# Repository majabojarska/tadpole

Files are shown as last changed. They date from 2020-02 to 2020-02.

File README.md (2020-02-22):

# Tadpole
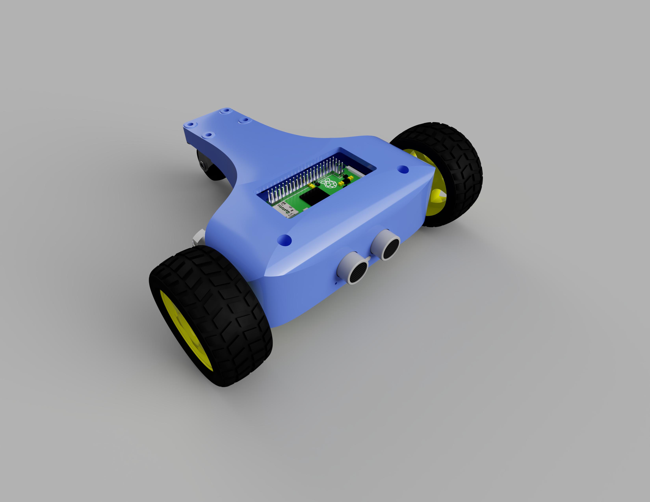
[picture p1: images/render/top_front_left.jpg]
Tadpole render


# About
Tadpole is a three-wheeled vehicle, driven by two indepedent front motors. My goal was to have a go at designing and integrating a system that consists of different software and hardware components.

A particularly interesting part of the design process, was implementing the motor controller logic, which handles conversion of user input, into motor speed and direction. The usage of two, independently driven front motors, enables the vehicle to not only turn while moving forwards/backwards, but also to spin in place. The calculated throttle (by default) is mapped to a 3rd order polynomial curve. This solution makes small movements result in subtle speed changes, but as the gamepad stick deviates further from its origin, the speed changes are more noticeable and aggressive. These characteristics make Tadpole particularly agile and precise.

## Hardware
Apart from te 3D printed stuff, the hardware parts are commonly available and can be cheaply ordered from online electronics shops. 

- Raspberry Pi Zero W
- 2x [6V DC motor](https://www.google.com/search?q=6v+dc+motor+robot+yellow).
- 2x 18650 battery.
- TP4056 battery charging and overdischarge protection module.
- DC-DC 5V booster module (RPi power source).
- DC-DC switching booster module (motor power source). 
- L9110S H-bridge motor driver.
- HC-SR04 ultrasonic sensor.
- Rotating furniture wheel.
- 3D printed frame.
- Xbox One S wireless gamepad.
- Some wires, soldering tools, screwdrivers, etc..

### 3D printing BOM
| Part ID | Amount (pcs)  |
| ---:|:---|
| cover_back.stl | 1 |
| cover_top.stl | 1 |
| frame_main.stl | 1 |
| mount_rpi.stl | 1 |

## Software
- [Raspbian Buster Lite](https://www.raspberrypi.org/downloads/raspbian/)
- [xpadneo](https://github.com/atar-axis/xpadneo) - Advanced Linux Driver for Xbox One Wireless Controller
- Python 3.6+ environment
- (optional) [Fusion 360, for tweaking the existing 3D project.](https://www.autodesk.com/products/fusion-360/overview)

## 3D Models
3D models are available in STL format under the [/models](./models) directory.
- Dummy models [/models/dummy](./models/dummy)
- Tadpole parts models [/models/tadpole](./models/tadpole)

## Circuit schematics
Circuit schematics in different file formats are located in the [/schematics](./schematics) directory.

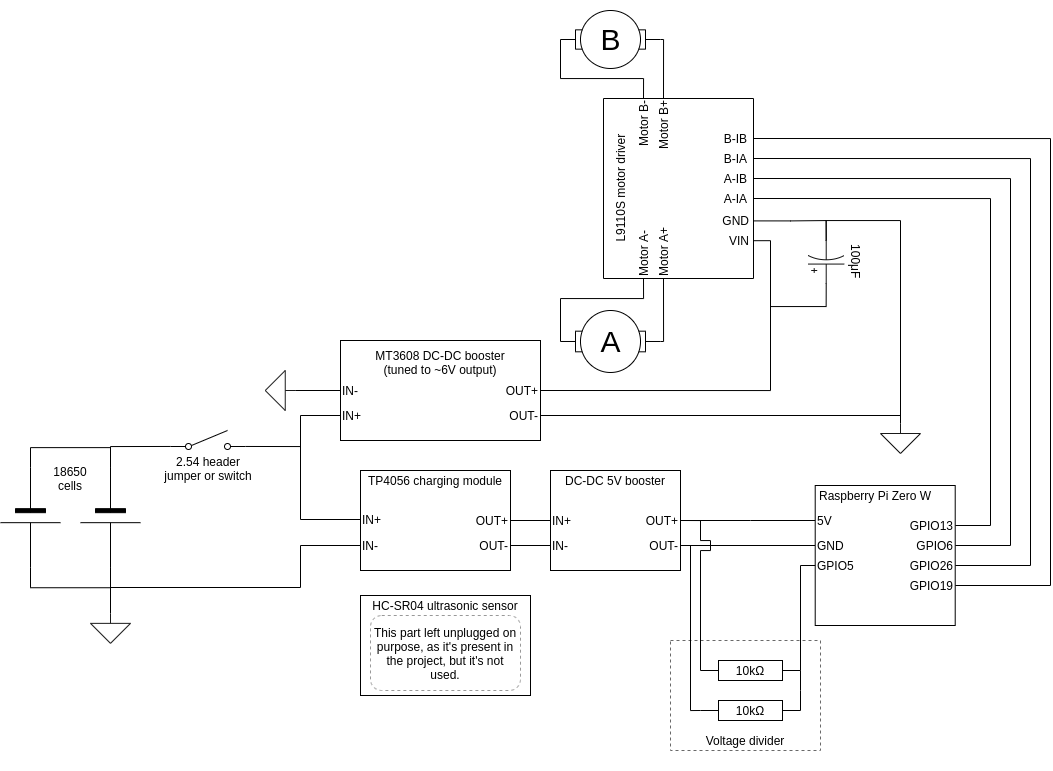
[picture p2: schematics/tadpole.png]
Tadpole schematic


## Images

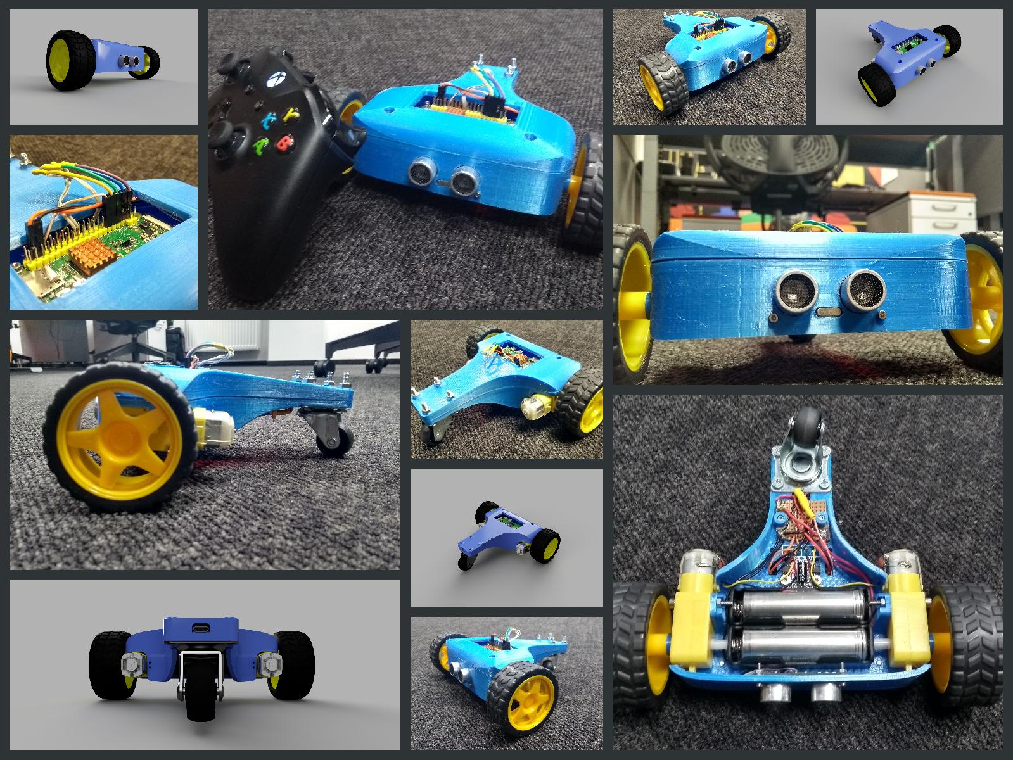
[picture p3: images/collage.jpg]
Tadpole images
Rendered images as well as real life photos can be found in the [images/](./images) directory.

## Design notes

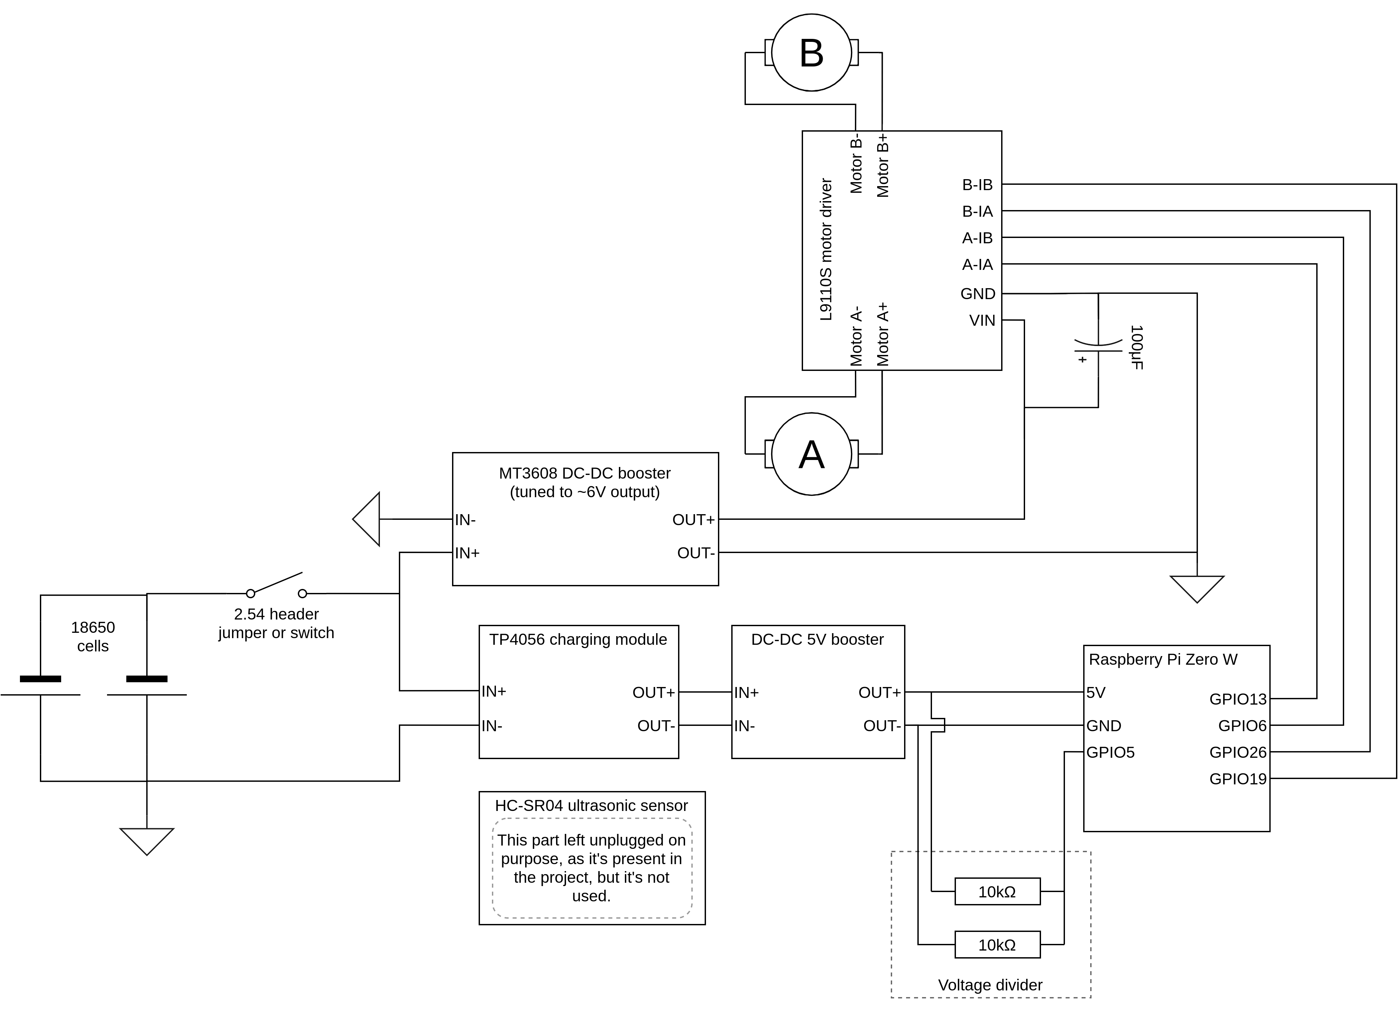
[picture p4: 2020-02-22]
schematics/tadpole_hi_res.png

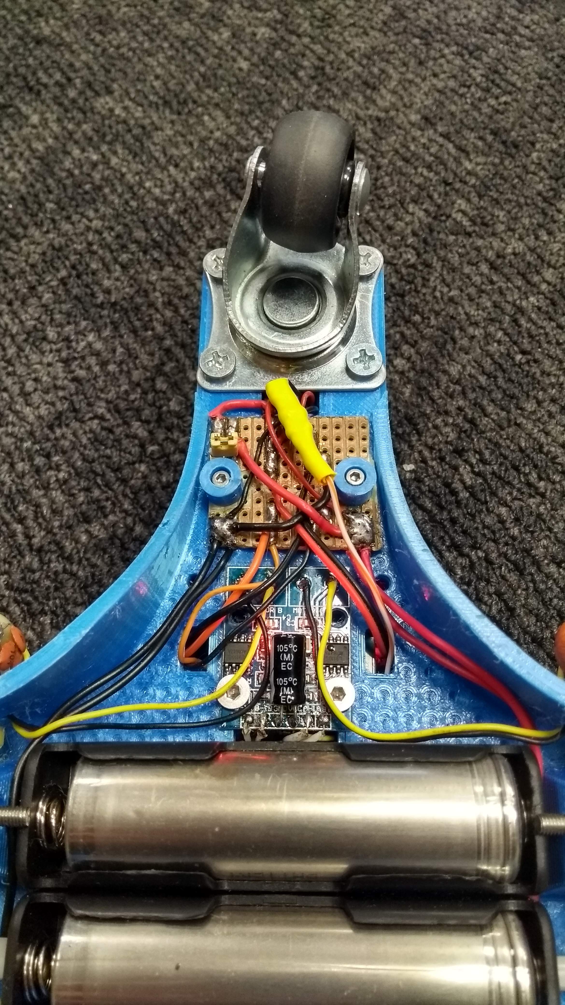
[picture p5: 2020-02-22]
images/photo/tadpole_14.jpg

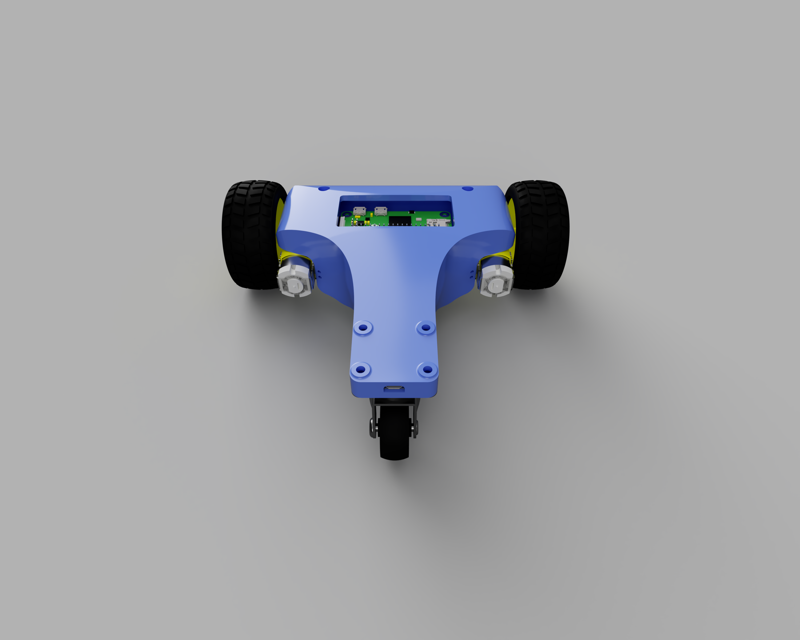
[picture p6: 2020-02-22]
images/render/top_back.png

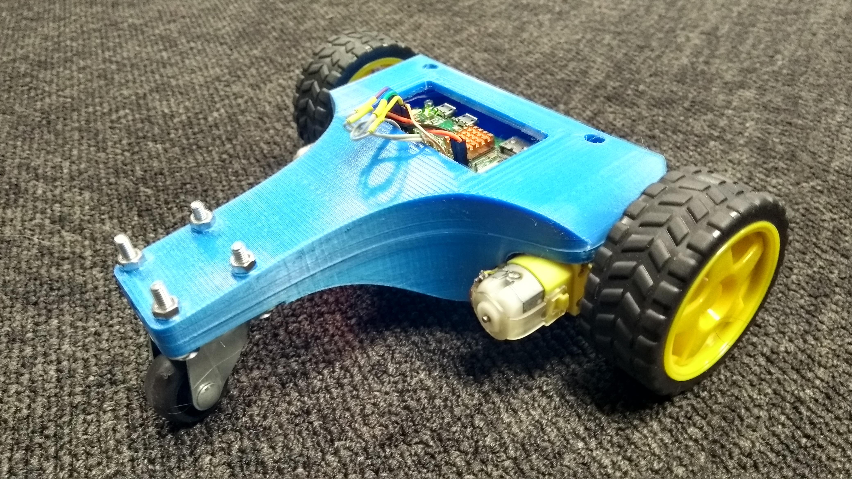
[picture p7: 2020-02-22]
images/photo/tadpole_07.jpg

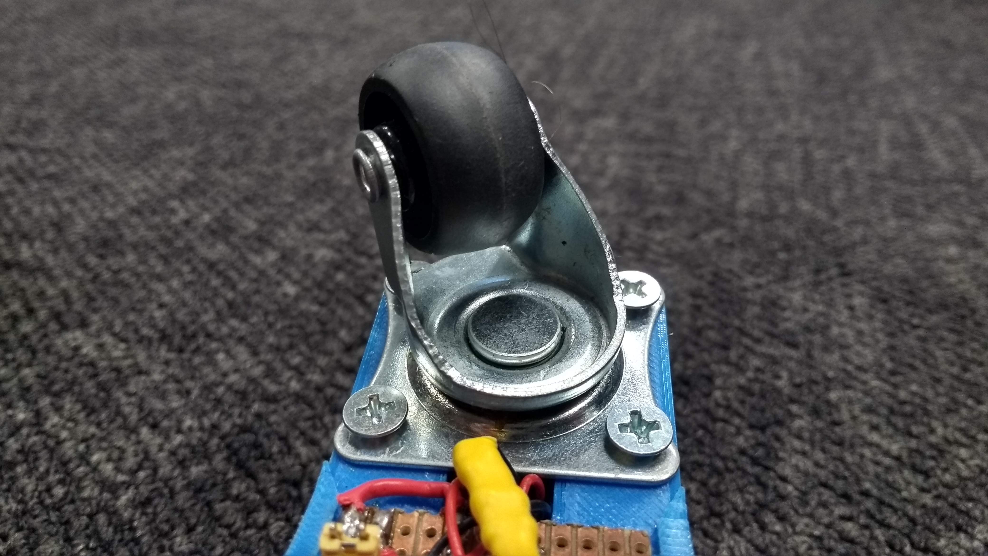
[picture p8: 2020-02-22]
images/photo/tadpole_17.jpg

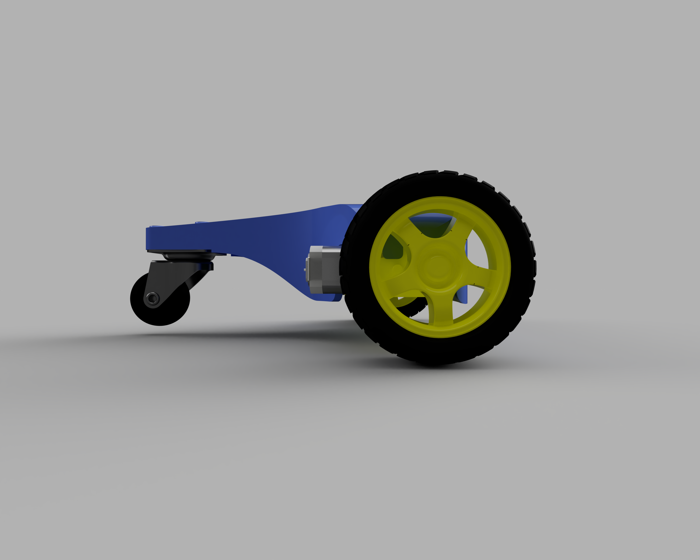
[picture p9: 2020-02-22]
images/render/right.png

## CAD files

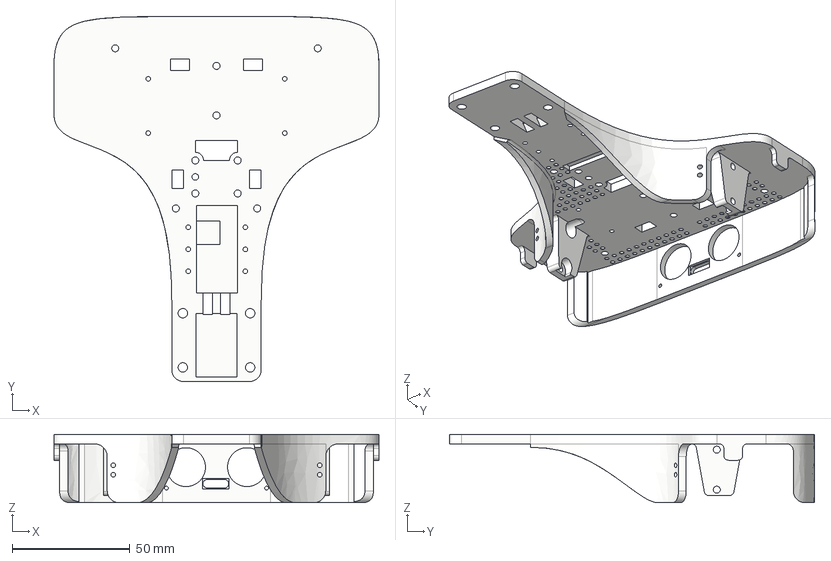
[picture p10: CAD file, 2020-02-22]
models/tadpole/step/frame_main.step
138.0 x 155.0 x 29.0 mm

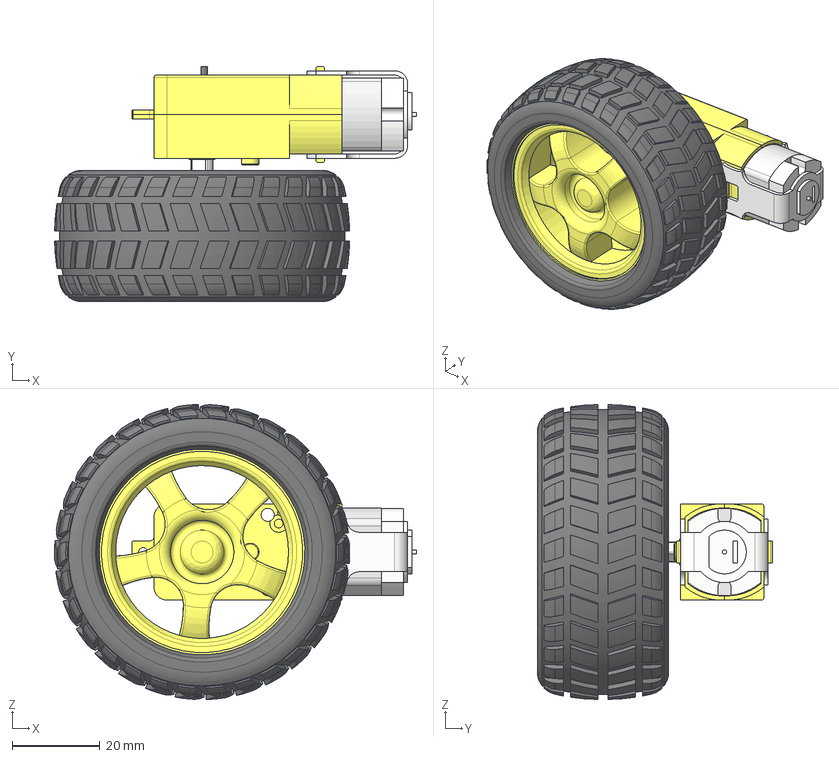
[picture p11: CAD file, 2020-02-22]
models/dummy/dc_motor_with_wheel.stp
82.7 x 53.8 x 67.5 mm
Wheel
capa 1 (amarela)
pino 2 (cinza)
capa 2 (amarela)
pino motor
base1 (cinza)
Ponta (preto)
suporte motor (acrílico)

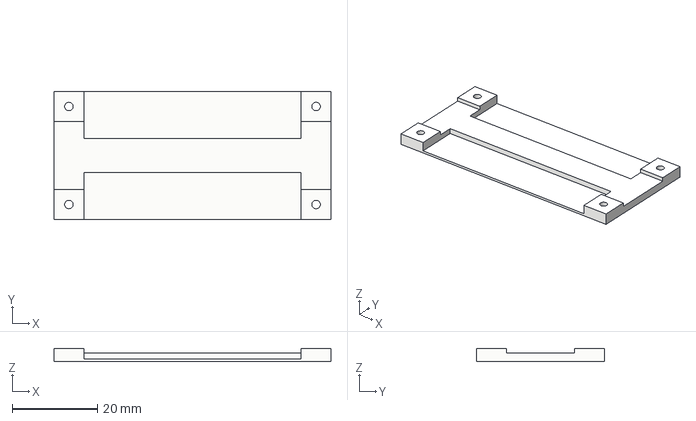
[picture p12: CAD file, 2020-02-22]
models/tadpole/step/mount_rpi.step
65.0 x 30.0 x 3.00 mm

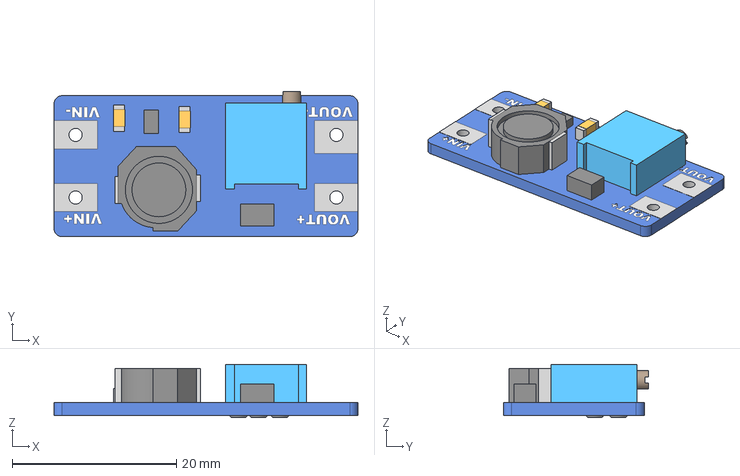
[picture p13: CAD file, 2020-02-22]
models/dummy/mt3608_module.stp
37.0 x 17.7 x 6.50 mm

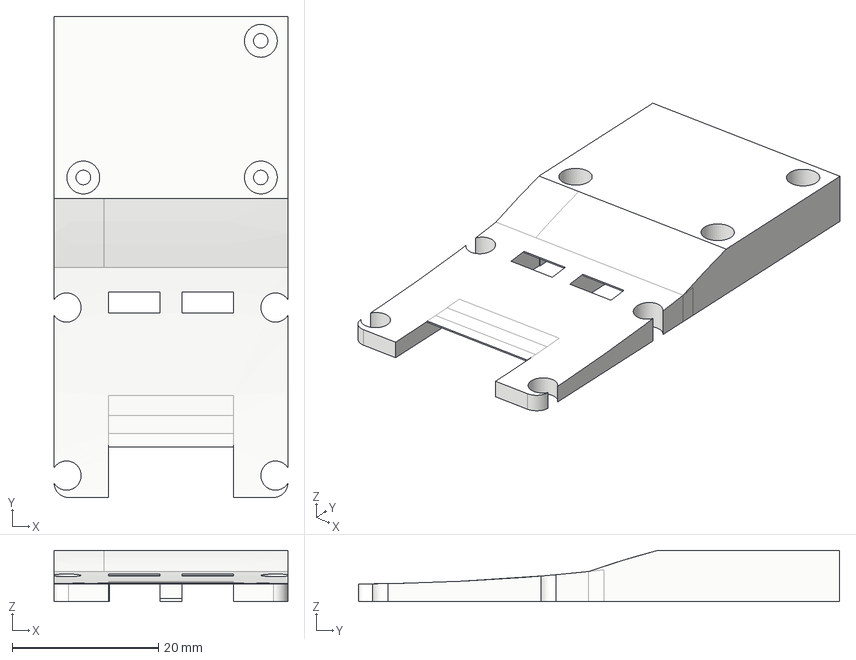
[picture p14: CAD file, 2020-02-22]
models/tadpole/step/cover_back.step
32.0 x 65.8 x 7.00 mm

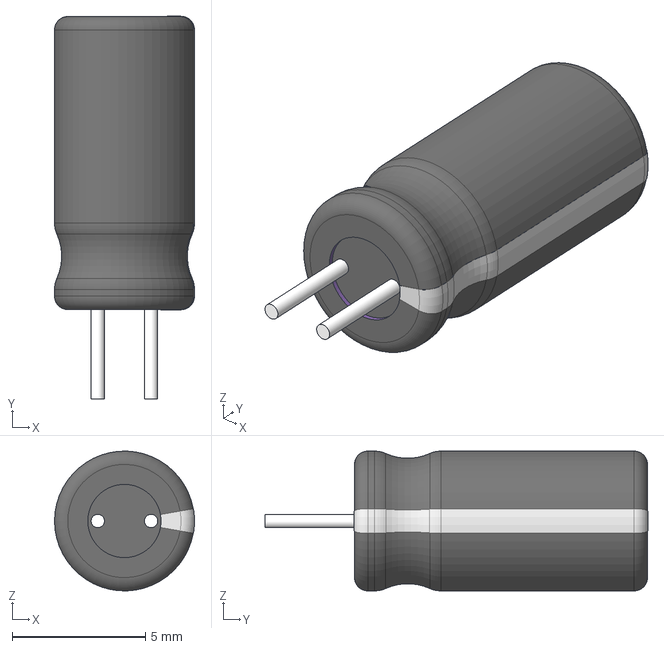
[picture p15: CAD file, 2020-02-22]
models/dummy/capacitor_electrolytic.stp
5.26 x 14.4 x 5.25 mm

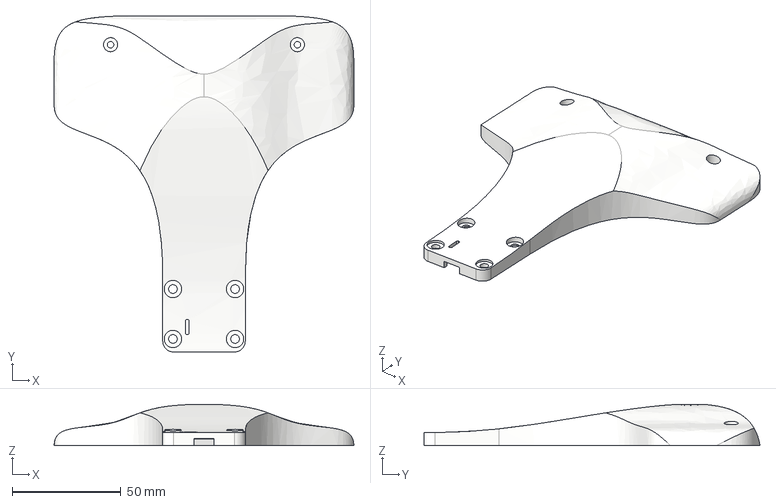
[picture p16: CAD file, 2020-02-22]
models/tadpole/step/cover_top.step
138.0 x 154.7 x 19.1 mm

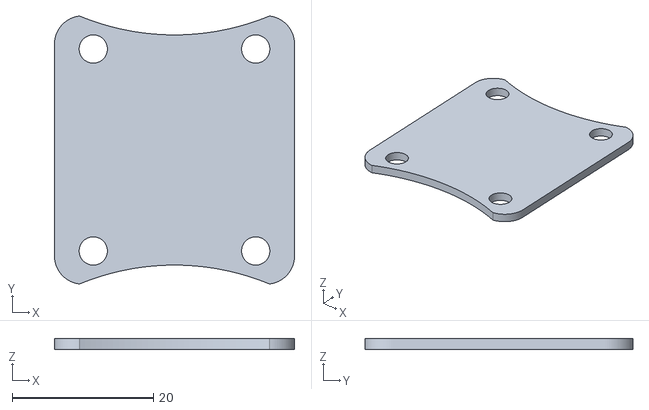
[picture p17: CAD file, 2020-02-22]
models/dummy/tail_wheel_plate.stl
34.0 x 38.0 x 1.50

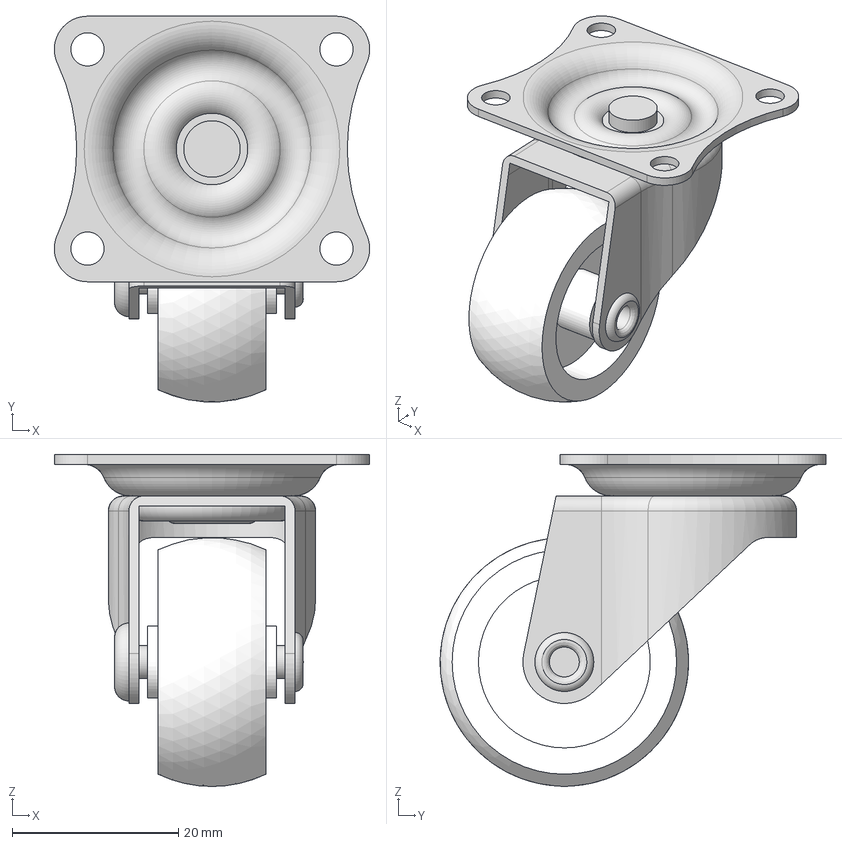
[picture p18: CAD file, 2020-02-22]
models/dummy/wheel_caster_swivel_40mm.stp
38.0 x 46.5 x 40.0 mm
Caster_40mm_Wheel_30mm_01
Caster_40mm_Wheel_support_01
Caster_40mm_Swivel_plate_01

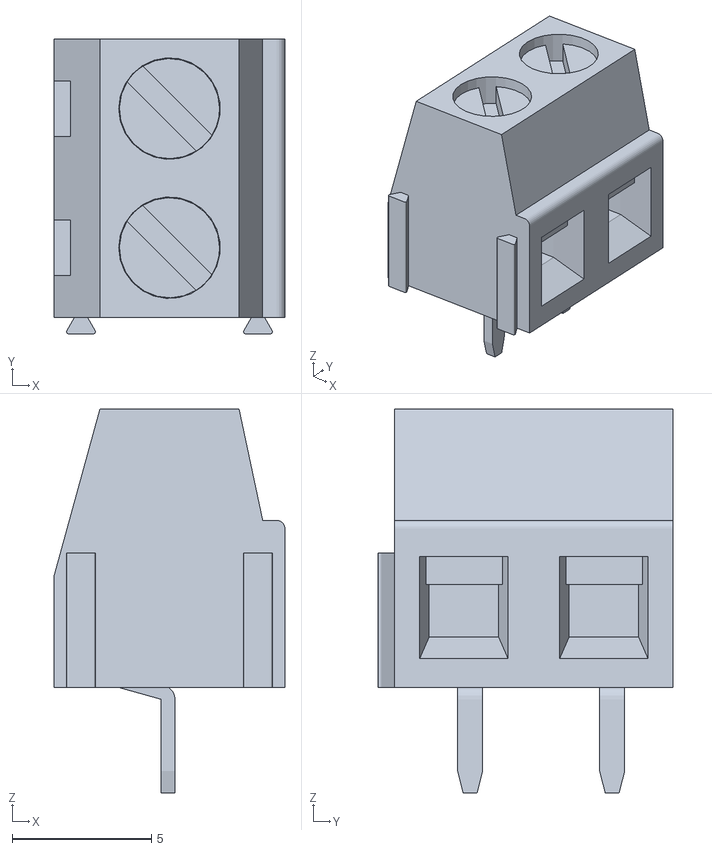
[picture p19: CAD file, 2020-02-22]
models/dummy/pcb_terminal_block_1x2.stl
8.30 x 10.6 x 13.8

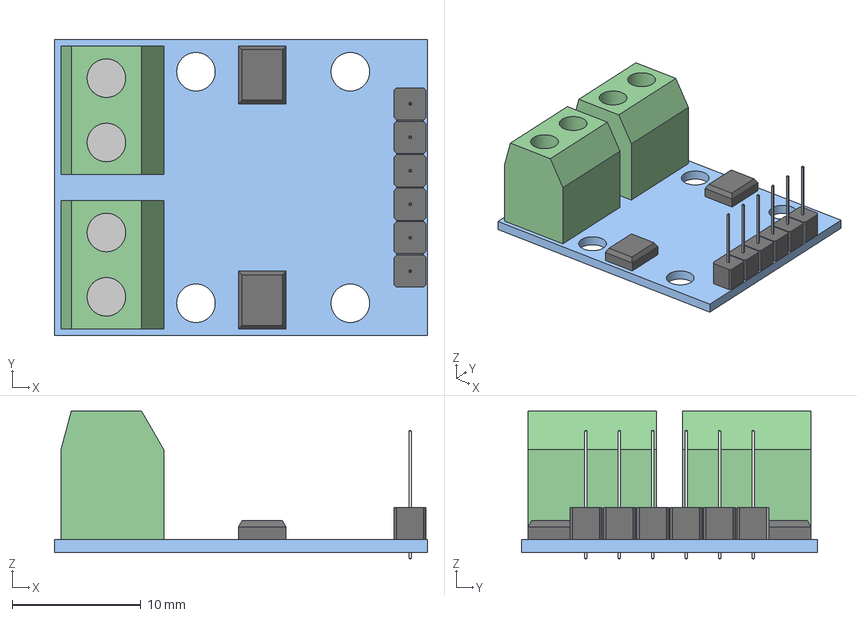
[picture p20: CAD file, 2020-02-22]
models/dummy/l9110s_motor_driver.stp
29.0 x 23.0 x 11.5 mm

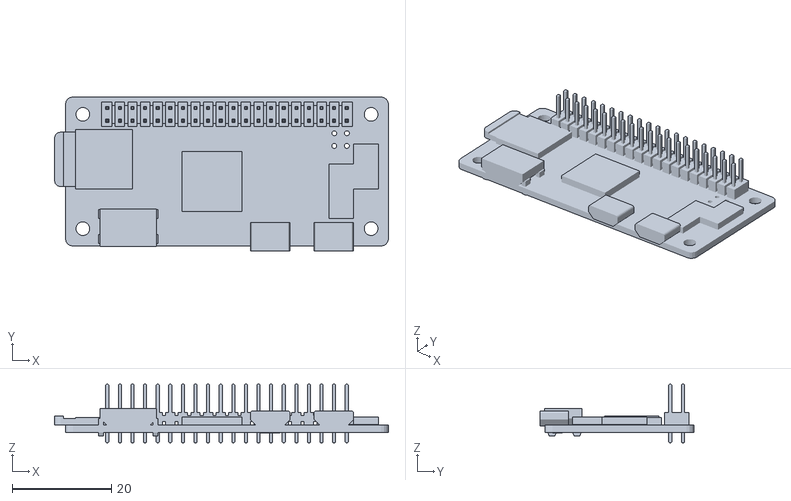
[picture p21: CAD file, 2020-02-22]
models/dummy/rpi_zero_combined.stl
67.2 x 31.0 x 11.8

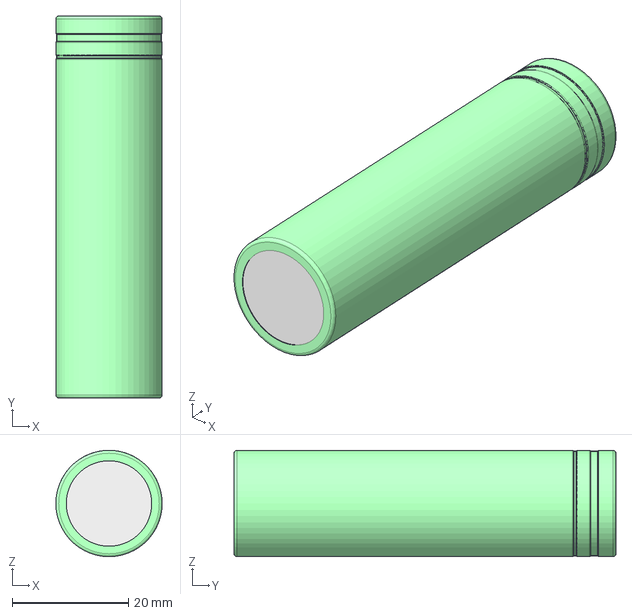
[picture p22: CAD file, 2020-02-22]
models/dummy/18650_cell.stp
18.3 x 65.8 x 18.3 mm

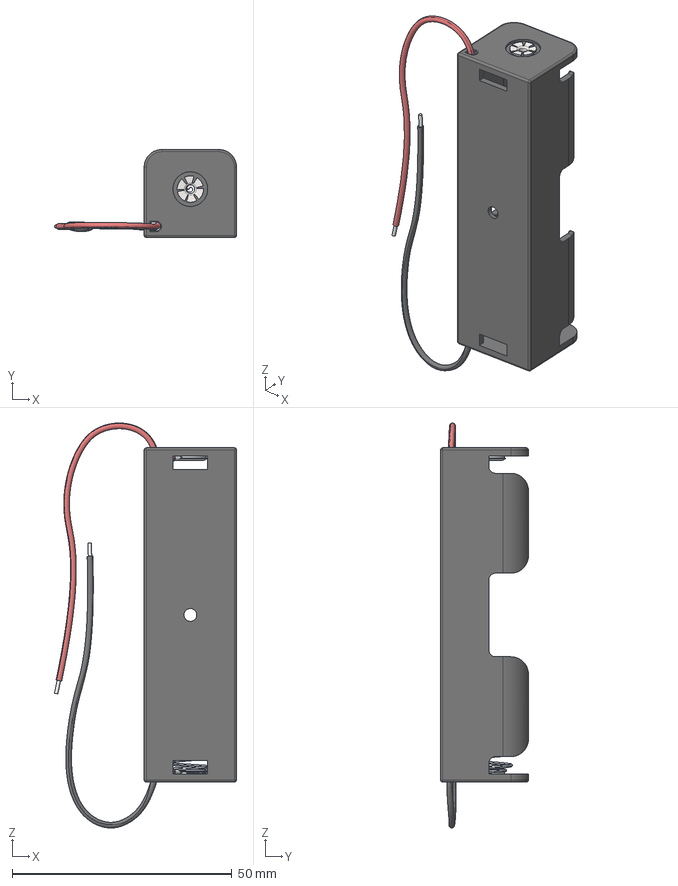
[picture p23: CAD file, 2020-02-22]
models/dummy/18650_holder.stp
41.4 x 20.0 x 92.0 mm

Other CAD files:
models/tadpole/stl/cover_back.stl
models/tadpole/stl/cover_top.stl
models/tadpole/stl/frame_main.stl
models/tadpole/stl/mount_rpi.stl

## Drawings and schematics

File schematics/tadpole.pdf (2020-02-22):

# BL9110S motor driver

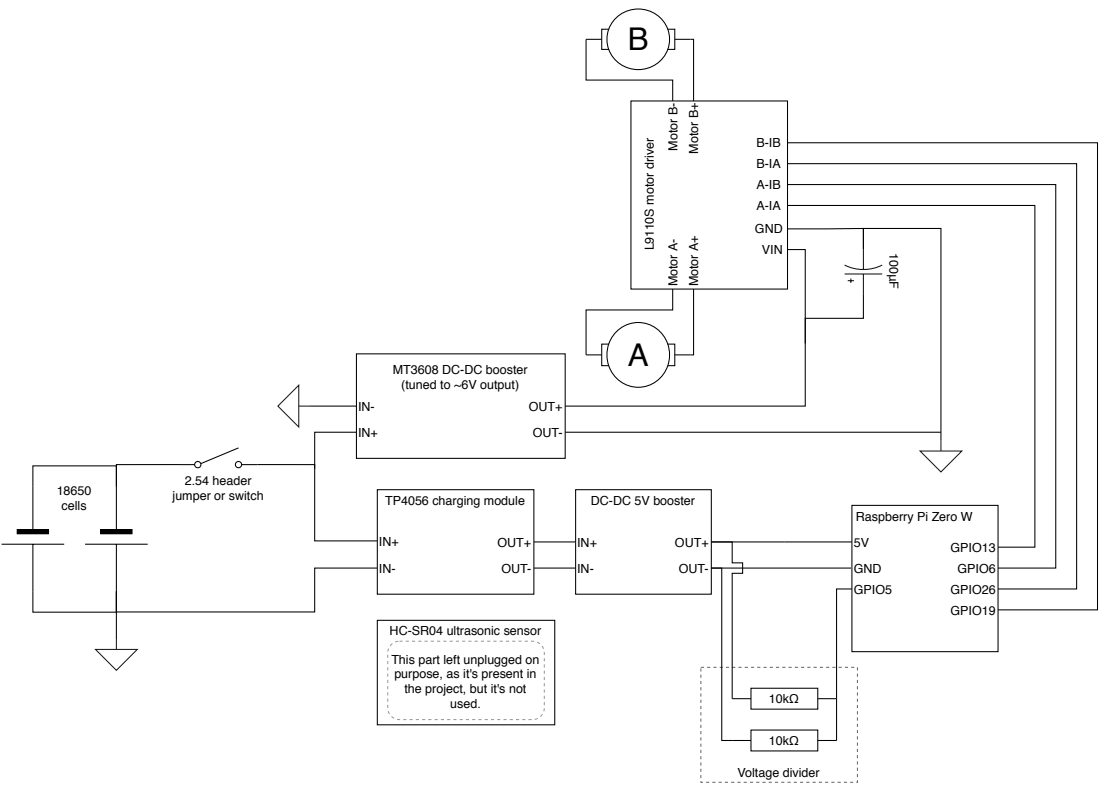
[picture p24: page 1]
used.; cells; TP4056 charging module; OUT+; OUT-; GND; GPIO13; GPIO6; GPIO26; GPIO19; GPIO5; Voltage divider; Motor A-; VIN

Motor A+ Motor B- Motor B+

MT3608 DC-DC booster
(tuned to ~6V output)

2.54 header
jumper or switch

DC-DC 5V booster

Raspberry Pi Zero W

HC-SR04 ultrasonic sensor

This part left unplugged on
purpose, as it's present in
the project, but it's not

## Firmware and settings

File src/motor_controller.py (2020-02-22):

import math
import typing

from . import motor


class MotorController:
    """ Class for controlling front motors.

    Motor pins are defined as BCM GPIO indices.
    """

    SQRT_OF_TWO = math.sqrt(2)

    LEFT_MOTOR_POSITIVE_GPIO = 13
    LEFT_MOTOR_NEGATIVE_GPIO = 6
    RIGHT_MOTOR_POSITIVE_GPIO = 26
    RIGHT_MOTOR_NEGATIVE_GPIO = 19

    MAX_ABS_AXIS_VALUE = 2 ** 15

    def __init__(
        self,
        enable_throttle_curve: bool = False,
        throttle_gate_threshold: float = 0.1,
        throttle_scale: float = 1.0,
        throttle_limit: float = 1.0,
    ) -> None:
        """

        Parameters
        ----------
        enable_throttle_curve : bool
            If True, a throttle curve will be used.
        throttle_gate_threshold : float
            Threshold of the throttle gate.
            Throttle will be applied only if it exceeds this value.
        throttle_scale : float
            The value by which the throttle will be scaled.
        throttle_limit : float
            The maximum value throttle can achieve after applying all other modifiers.
        """
        self.left_motor = motor.Motor(
            self.LEFT_MOTOR_POSITIVE_GPIO,
            self.LEFT_MOTOR_NEGATIVE_GPIO,
            is_reversed=True,
        )
        self.right_motor = motor.Motor(
            self.RIGHT_MOTOR_POSITIVE_GPIO, self.RIGHT_MOTOR_NEGATIVE_GPIO
        )

        self.enable_throttle_curve = enable_throttle_curve

        self.throttle_gate_threshold = throttle_gate_threshold
        self.throttle_scale = throttle_scale
        self.throttle_limit = throttle_limit

    def handle_vector_input(self, input_vector: typing.Tuple[int, int]) -> None:
        """ Calculates and sets the throttle of both motors based on the input vector.

        Input vector processing chain is as follows:
        IN--->[Scale]->[Gate]->[Limit]--->OUT

        Parameters
        ----------
        input_vector : list
            A list of two integer values in the range of [0;65535].
        """
        angle = MotorController.calc_vector_angle(input_vector)
        left_motor_throttle_modifier = self.calc_left_throttle_mod(angle)
        right_motor_throttle_modifier = self.calc_right_throttle_mod(angle)
        throttle = self.throttle_scale * self.calc_normalized_vector_length(
            input_vector
        )

        if self.enable_throttle_curve:
            throttle = self._apply_throttle_curve(throttle)
        if self.throttle_gate_threshold is not None:
            throttle = self._apply_throttle_gate(throttle)
        if self.throttle_limit is not None:
            throttle = self._apply_throttle_limiting(throttle)

        left_motor_throttle = throttle * left_motor_throttle_modifier
        right_motor_throttle = throttle * right_motor_throttle_modifier

        self.left_motor.change_throttle(left_motor_throttle)
        self.right_motor.change_throttle(right_motor_throttle)

    def stop(self):
        """
        Stops both motors.

        :return: None
        """
        self.left_motor.stop()
        self.right_motor.stop()

    @staticmethod
    def calc_left_throttle_mod(joystick_angle: float) -> float:
        """ Calculates left motor throttle modifier.

        Function visualization: https://www.desmos.com/calculator/rhvsokblhl

        Parameters
        ----------
        joystick_angle : float
            The angle of the joystick with respect to the positive x axis.

        Returns
        -------
        throttle_modifier : float
            Throttle modifier for the left motor.
        """
        MotorController._assert_angle_within_range(joystick_angle)

        throttle_modifier = None
        if -180 < joystick_angle <= -90:
            throttle_modifier = -1.0
        elif -90 < joystick_angle < 0:
            throttle_modifier = joystick_angle / 45 + 1
        elif 0 <= joystick_angle <= 90:
            throttle_modifier = 1.0
        elif 90 < joystick_angle <= 180:
            throttle_modifier = -joystick_angle / 45 + 3

        return throttle_modifier

    @staticmethod
    def calc_right_throttle_mod(joystick_angle: float) -> float:
        """ Calculates right motor throttle modifier.

        Function visualization: https://www.desmos.com/calculator/xfo4g4fh4j

        Parameters
        ----------
        joystick_angle : float
            The angle of the joystick with respect to the positive x axis.

        Returns
        -------
        throttle_modifier : float
            Throttle modifier for the right motor.
        """

        MotorController._assert_angle_within_range(joystick_angle)

        throttle_modifier = None
        if -180 < joystick_angle < -90:
            throttle_modifier = -joystick_angle / 45 - 3
        elif -90 <= joystick_angle <= 0:
            throttle_modifier = -1.0
        elif 0 < joystick_angle < 90:
            throttle_modifier = joystick_angle / 45 - 1
        elif 90 <= joystick_angle <= 180:
            throttle_modifier = 1.0

        return throttle_modifier

    def calc_normalized_vector_length(
        self, input_vector: typing.Tuple[int, int]
    ) -> float:
        """ Calculates a normalized Euclidean vector length.

        Parameters
        ----------
        input_vector : tuple
            a tuple of two integer values representing a vector with
            initial point at (0,0) and a specified terminal point.

        Returns
        -------
        normalized_length : float
            Length of the normalized input vector.
        """

        assert type(input_vector) == tuple
        assert len(input_vector) == 2

        length = math.sqrt(input_vector[0] ** 2 + input_vector[1] ** 2)
        normalized_length = length / self.MAX_ABS_AXIS_VALUE
        if normalized_length > 1:
            normalized_length = 1

        return normalized_length

    @staticmethod
    def calc_vector_angle(input_vector: typing.Tuple[int, int]) -> float:
        """ Calculates the angle between the positive x axis and the input vector.

        Parameters
        ----------
        input_vector : tuple
            a tuple of two integer values representing a vector with
            initial point at (0,0) and a specified terminal point.

        Returns
        -------
        float
            vector angle as degrees in range (-180;180]
        """
        radians = math.atan2(input_vector[1], input_vector[0])
        return math.degrees(radians)

    @staticmethod
    def _assert_angle_within_range(angle: float) -> None:
        """ Asserts that the input angle is within a valid range of [-180;180) degrees.

        Parameters
        ----------
        angle : float
            Input angle.

        Raises
        ------
        ValueError
            If angle <= -180 or angle > 180.
        """
        if angle <= -180 or angle > 180:
            raise ValueError("Input angle is out of permitted range (-180;180]")
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

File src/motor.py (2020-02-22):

import logging

import RPi.GPIO as GPIO

logging.getLogger(__name__)


class Motor:
    """ Class for controlling a single motor over an H-bridge.

    Attributes
    ----------
    gpio_positive : int
        GPIO pin number of the positive motor control terminal.
    gpio_negative : int
        GPIO pin number of the negative motor control terminal.
    is_reversed : bool
        Defines whether the motor rotation direction is reversed.
    throttle : int
        Current throttle value.
    self.pwm_positive : int
        Current PWM value on gpio_positive pin.
    self.pwm_negative : int
        Current PWM value on gpio_negative pin.
    """

    def __init__(self, gpio_positive, gpio_negative, is_reversed=False):
        """
        Parameters
        ----------
        gpio_positive : int
            GPIO pin number of the positive motor control terminal.
        gpio_negative : int
            GPIO pin number of the negative motor control terminal.
        is_reversed : bool
            Defines whether the motor rotation direction is reversed.
        """
        self.gpio_positive = gpio_positive
        self.gpio_negative = gpio_negative
        self.is_reversed = is_reversed

        self.throttle = 0

        GPIO.setmode(GPIO.BCM)

        # Initialize and start PWM
        GPIO.setup(self.gpio_positive, GPIO.OUT)
        GPIO.setup(self.gpio_negative, GPIO.OUT)
        self.pwm_positive = GPIO.PWM(self.gpio_positive, 100)
        self.pwm_negative = GPIO.PWM(self.gpio_negative, 100)
        self.pwm_positive.start(0)
        self.pwm_negative.start(0)

    def __del__(self):
        """ Stops motor before object deletion """
        self.stop()

    def change_throttle(self, throttle) -> None:
        """ Sets a duty cycle based on the throttle parameter.

        Parameters
        ----------
        throttle : float
            New throttle value, between -1.0 and 1.0.
        """
        if self.is_reversed:
            throttle *= -1

        self.throttle = throttle

        abs_duty_cycle = round(abs(throttle) * 100)

        if throttle >= 0:
            self.pwm_positive.ChangeDutyCycle(abs_duty_cycle)
            self.pwm_negative.ChangeDutyCycle(0)
        else:
            self.pwm_positive.ChangeDutyCycle(0)
            self.pwm_negative.ChangeDutyCycle(abs_duty_cycle)

    def stop(self) -> None:
        """ Stops motor by setting both PWM duty cycles to 0 """
        logging.info("{} - Stopping motor".format(__name__))
        self.pwm_positive.ChangeDutyCycle(0)
        self.pwm_negative.ChangeDutyCycle(0)

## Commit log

2020-02-22 Initialize project repo
    [18650_cell.stp, 18650_holder.stp, capacitor_electrolytic.stp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]
2020-02-22 Fix MT3608 GND connection
